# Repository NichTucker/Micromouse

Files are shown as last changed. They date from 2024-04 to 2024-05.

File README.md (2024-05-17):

# Micromouse
## Overview
Welcome to our Micromouse project repository. This repository contains all the necessary files and documentation related to our project, including PCB design files, reports, etc..

## Project Description
Our project involves designing the power subsystem and the sensing subsystem for the micromouse, which is essentially a maze-solving robot. We are focusing on designing the hardware components.

## Subsystems
### Power Subsystem
Responsible for powering and controlling the power supplied to the entire system, running the motors of the micromouse and charging the battery that powers the mouse.
### Sensing Subsystem
The sensor subsystem is responsible for detecting objects and ensuring that the micromouse maintains proper alignment within the maze pathways by sensing the walls around it.

The sensing subsystem folder contains all the necessary files and documentation for the design and implementation of the sensor subsystem. These being the datasheets of the non-passive components used, LaTeX and PDF design report, KiCad schematics and files, the gerber files and the code used to test if the micromouse can sense walls to the left, right and front of it.

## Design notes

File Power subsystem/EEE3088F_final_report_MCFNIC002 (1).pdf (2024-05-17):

# Interim Design Report

Micromouse Power Subsystem


Prepared by:
Nicholas McFarland
MCFNIC002

Prepared for:
EEE3088F
Department of Electrical Engineering University of Cape Town

May 17, 2024

# Declaration

1. I know that plagiarism is wrong. Plagiarism is to use another’s work and pretend that it is one’s own.
2. I have used the IEEE convention for citation and referencing. Each contribution to, and quotation in, this report from the work(s) of other people has been attributed, and has been cited and referenced.
3. This report is my own work.
4. I have not allowed, and will not allow, anyone to copy my work with the intention of passing it off as their own work or part thereof.

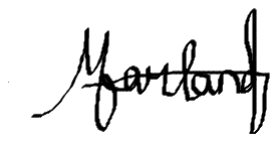
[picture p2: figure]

May 17, 2024

Nicholas McFarland | Date

ii

# Contents

1 Introduction | 1
2 Requirements Analysis | 2
3 Subsystem Design | 5
4 Acceptance Testing | 11
5 Conclusion | 18
Bibliography | 19

iii

# Chapter 1

# Introduction

### 1.1 Problem Description

This year’s design project aims to have a pair of students design and build a micromouse capable of solving a maze. The mouse begins at a starting position outside of the maze and is considered to have ‘solved’ the maze if it reaches the square opening in the middle of the maze.

Figure 1.1: Typical maze that a micromouse should be able to solve

The mouse’s final design consists of a motherboard, processor board, motors, wheels, power, and sensing subsystem. Both the motherboard and processor board will be responsible for most of the mouse’s information processing. The power and sensing subsystems are not provided, and so still need to be designed. The motherboard, processor board, wheels, and motors are provided by the course.

This report provides an in-depth analysis of the designed power subsystem, which is responsible for providing power to all the aforementioned systems and subsystems, as well as driving the motors of the mouse.

### 1.2 Scope and Limitations

The designed circuit board uses a single 1S1P battery to power all parts of the system of the micromouse. It must be able to operate 2 motors at rated current and voltage and provide an analog connection that provides information to the processor regarding the battery’s current voltage and charge state. It must be able to charge the battery from an external 5V input voltage and house an ON/OFF switch that can control the power supply to the system.

Besides the connections between the power subsystem’s pin headers and motherboard, this project provides no detail into the other subsystems of the overall micromouse. It does not provide any coding required to operate the other subsystem/s.

The shape of the PCB design must feature a tab with dimensions that prevent it from obstructing the motor connections or colliding with any of the motherboard connections. The design consists of a battery with a maximum voltage of 4.2V, so any selected component cannot have an operating voltage that exceeds this. The cost of producing 2 boards may not exceed $30 when ordered, so the cost per board may not exceed $15. All components selected for designing the system must be readily available on JLCPCB [1]. Finally, the design must be suitable for testing any potential problem points on the board and feature alternative options to prevent these problems.

### 1.3 GitHub Link

https://github.com/NichTucker/Micromouse

# Chapter 2

# Requirements Analysis

### 2.1 Requirements

The requirements for a micromouse power module are described in Table 2.1.

Table 2.1: User and functional requirements of the power subsystem.

Req. ID | Description
R01SWT | Design must be able to switch the micromouse ON and OFF
R02SWT | When the mouse is OFF, current drawn by battery < 500uA
R01PWR | Design powers the entire micromouse and drive the 2 motors used to drive the wheels
R01CHG | Charge the battery from an input pin
R02CHG | Recommended charge at 0.5C (Capacity) for battery
R01ADC | Provides information on the battery’s voltage and sense of state of charge (SoC)
R01PCB | Design must be able to fit on the motherboard without colliding with any of the other
| systems or the motors

### 2.2 Specifications

The specifications, refined from the requirements in Table 2.1, for the micromouse power module are described in Table 2.2.

Table 2.2: Specifications of the power subsystem derived from the requirements in Table 2.1.

Spec. ID | Description
S01SWT | Design utilizes a physical switch to provide the mouse with the ability to connect and
| disconnect the battery from the rest of the mouse
S02SWT | When the switch is in its OFF state and the battery is disconnected from the circuit, the
| current drawn by the battery must be < 500uA
S01PWR | Design uses the Battery LiPo 800mAh 3.7V (https://www.robotics.org.za/802540) to power all the systems of the micromouse and
| uses a dual bridge motor to operate the motors, each rated at 200mA and 3.7V
S01CHG | Circuit uses a Li-Po battery charger with a 5V operating input voltage
S02CHG | Drawn current < 400mA when charging
S01ADC | Voltage divider circuit to provide batter’s state of charge (SoC), as well as ensure the
| maximum input voltage < 3.3V
S01PCB | 2x8 pin header with 2.54mm pin pitch. The height of the tab > 18mm and the width of the
| tab < 35mm to prevent collision with the motors

2.3. Testing Procedures

### 2.3 Testing Procedures

A summary of the testing procedures [2] detailed in chapter 4 is given in Table 2.3.

Table 2.3: Testing Procedures

Testing ID | Description
AT01SWT | Switch provides discreet ON/OFF states
AT02SWT | Quiescent current less than maximum rated
AT01PWR | Each motor reaches its operating current of 200mA
AT02PWR | Each motor reaches its operating voltage of 3.7V
AT01CHG | Charging circuit charges battery
AT02CHG | Battery draws < 400mA when charging and the rest of the
| circuit is connected
AT01ADC | Pin M210 (BATT_ADC) provided with scaling analog volt-
| age
AT01PCB | Height and width of PCB tab smaller than area limited by
| motor.

### 2.4 Traceability Analysis

To show how the requirements, specifications and testing procedures all link, Table 2.4 is provided.

Table 2.4: Requirements Traceability Matrix

# | Requirements | Specifications | Acceptance Test

1 2 3 4 5 6 7 8 | R01SWT R02SWT R01PWR R01BAT R01CHG R02CHG R01ADC R01PCB | S01SWT S02SWT S01PWR S01BAT S01CHG S02CHG S01ADC S01PCB | AT01SWT AT02SWT AT01PWR, AT02PWR AT01BAT AT01CHG AT02CHG AT01ADC AT01PCB

### 2.4.1 Traceability Analysis 1

From R01SWT, the design must be able to switch the micromouse on and off. This is where S01SWT is derived, as it refines R01SWT to incorporate a physical switch to turn the micromouse on and off. This can be tested through AT01SWT, which tests that the design can disconnect the battery from the rest of the circuit, providing discreet ON/OFF states.

### 2.4.2 Traceability Analysis 2

R02SWT states that the current drawn by the battery when the mouse is off must be < 500uA. From this S02SWT specifies that this is the current in the case when the switch is off and the battery is

2.4. Traceability Analysis

disconnected from the circuit. This current is tested through AT02SWT, which is implemented to measure the quiescent current of the subsystem.

### 2.4.3 Traceability Analysis 3

From R01PWR the design must be able to power the entire micromouse and drive the motors. S01PWR builds on this, specifying that the design must use the Battery LiPo 800mAh 3.7V (https://www.robotics.org.za/802540) to provide power to the different systems and should use a dual H-bridge motor driver to operate the motors. These are tested through AT01PWR and AT02PWR, which test that the motors reach their correct operating currents and voltages.

### 2.4.4 Traceability Analysis 4

R01CHG states that the design must be able to charge the battery from an input pin. From this S01CHG can be derived as it provides more insight into the charging. It must use a Li-Po battery charger with a 5V operating input voltage, as this will be the provided charging voltage by the STM. This is tested by AT01CHG which tests that the circuit can charge the battery.

### 2.4.5 Traceability Analysis 5

From R02CHG, since the battery must charge at 0.5C, S02CHG is derived as it specifies that to meet this requirement the battery must draw < 400mA when charging and still be connected to the rest of the circuit. This is tested through AT02CHG, where the charging current is measured.

### 2.4.6 Traceability Analysis 6

R01ADC requires the design to provide information on the battery’s current voltage and state of charge. S01ADC provides more insight into this, describing the means to which this is met and that the maximum analog voltage < 3.3V. This is tested through AT01ADC, where this voltage is measured to ensure that it scales correctly.

### 2.4.7 Traceability Analysis 7

From R01PCB the design must be able to fit on the motherboard without any collisions. S01PCB is derived from this and provides more detail as to the specified dimensions that the PCB must be to prevent any collisions. This is tested through AT01PCB, which tests that the dimensions of the PCB are smaller than the area limited by the motors.

# Chapter 3

# Subsystem Design

### 3.1 Design Decisions

### 3.1.1 Final Design

*From component browsing on JLCPCB it was found that the 0603 package resistors and capacitors were abundantly stocked, so

unless explicitly stated otherwise all resistors and capacitors were selected from these packages.*

Motor Driver

To turn the wheels the power subsystem requires a circuit design to drive the motors. Normally it would be easiest to drive the motor with a solo H-bridge, but with 2 motors needing to be driven simultaneously, this would not suffice. If the motors are to be driven at the same speed, each H-bridge would need identical voltages. This is practically impossible to achieve with 2 H-bridges, but this problem is solved if a dual H-bridge is used instead.

When checking JLCPCB, the options for dual H-bridge motor drivers were extremely limited, as most of the components

had low stock. The only ones that had enough stock to even consider using were the DRV8833 drivers. This, in conjunction

with their datasheets made the DRV8833s the best option for driving the micromouse. The selection process below

consists of tabulated potential choices from JLCPCB and selecting the most viable option:

Table 3.1: Dual bridge motor driver ICs

Possible solu-tion | Rated Supply Voltage (V) | Rated Supply Current (A) | Price per IC($) | Availability | Dimensions (mm x mm)
DRV8833PWP (https://wmsc.lcsc.com/wmsc/upload/file/pdf/v2/lcsc/2303020200_Texas-Instruments-DRV8833PWP_C1556089.pdf) | 2.7 - 10.8 | 1.5 | 1.1790 | 27 | 5 x 6
DRV8833PWPR (https://wmsc.lcsc.com/wmsc/upload/file/pdf/v2/lcsc/1810151712_Texas-Instruments-DRV8833PWPR_C50506.pdf) | 2.7 - 10.8 | 1.5 | 0.6660 | 9631 | 5 x 6
DRV8833RTYR (https://wmsc.lcsc.com/wmsc/upload/file/pdf/v2/lcsc/1810010132_Texas-Instruments-DRV8833RTYR_C154936.pdf) | 2.7 - 10.8 | 1.5 | 1.185 | 1315 | 4 x 4

from Table 3.1, the DRV8833PWPR (https://wmsc.lcsc.com/wmsc/upload/file/pdf/v2/lcsc/1810151712_Texas-Instruments-DRV8833PWPR_C50506.pdf) was chosen, because of the following:

- Meets the required rated voltage and current
- Much cheaper option than option 1 and option 3
- Readily available (higher stock than 1 and 3)
- The datasheet provides a typical circuit diagram of how to implement the device

*Note that the DRV8833PWPR (https://wmsc.lcsc.com/wmsc/upload/file/pdf/v2/lcsc/1810151712_Texas-Instruments-DRV8833PWPR_C50506.pdf) IC’s datasheet provides a suitable circuit schematic for setting up the driver’s connections.*

All capacitors were chosen at E24 values and added to prevent any AC noise from interfering with the motor driver circuit.

3.1. Design Decisions

Battery Management

The power subsystem requires battery-charging capabilities to charge the battery powering the rest of the mouse. Due to the requirements of the design the charger can only be powered by a 5V supply. This was taken into account when selecting potential solutions.

The easiest way to implement this charging is with a battery-charger IC. Using one of these, instead of designing one from scratch provides a much more reliable, stable and safe charge to the battery.

Once again, when looking at the options on JLCPCB, most of the charger ICs were too low stocked to even be considered,

but the TP4056 family provided ICs that operated at the required voltages (4.2V maximum battery charge voltage

charged with a 5V input) and were readily stocked at the time of ordering. The following ICs were considered for the

design:

Table 3.2: battery management ICs

Possible solution | JLCPCB part # | Rated Input Voltage (V) | Quietient current/Iq (uA) | Price per IC($) | Availability | Dimensions (mm x mm)
TP4056 | C725790 (https://wmsc.lcsc.com/wmsc/upload/file/pdf/v2/lcsc/2311091738_UMW-Youtai-Semiconductor-Co---Ltd--TP4056_C725790.pdf) | 4.0 - 6.5 | 35 | 0.0620 | 29409 | 4 x 5
TP4056 | C17702041 (https://wmsc.lcsc.com/wmsc/upload/file/pdf/v2/lcsc/2309121405_HXY-MOSFET-TP4056_C17702041.pdf) | 4.5 - 8.0 | 55 | 0.0587 | 10658 | 5 x 5
TP5000X-4.2-ESOP8 | C5447152 (https://wmsc.lcsc.com/wmsc/upload/file/pdf/v2/lcsc/2304251410_TOPPOWER-Nanjing-Extension-Microelectronics-TP5000X-4-2-ESOP8_C5447152.pdf) | 4.0 - 9.0 | 180 | 0.2465 | 5022 | 5 x 6

From Table 3.2, the first solution (C725790) was chosen. The reasons are as follows:

- Cheaper than option 2.
- Largest available supply.
- Smallest component (reduces PCB size).
- Lowest Iq ensures lowest possible current when mouse is active.

The charging current is controlled by the Rprog resistor. From the given equation in the datasheet:

Ibat =

Vprog

Rprog

1200

Setting Rprog at 1600 Ω ensures Ibat is (750mA) which is less than the maximum rated current (1A) and that the resistor is of E24 value. The rest of the circuit was designed with the aid of a typical charging circuit on the datasheet of a similar IC [TP4056]. (https://dlnmh9ip6v2uc.cloudfront.net/datasheets/Prototyping/TP4056.pdf)

*The selected IC has built-in voltage regulation and protection, so this was not needed in the design

Analog Sensing

This consists of a voltage divider circuit that reduces the battery’s read voltage to a maximum of 3V3 (ADC pin’s required voltage).
Since the battery has a maximum of 4.2V, simply feeding this into the ADC pin could break it, so the divider circuit must ensure Vout ≤ 3.3V. from the equation of a voltage divider:

Vout = Vin

R7
R5 + R7

Setting R5 = 10KΩ and R7 = 33KΩ, Vout is set at 3.22V which is safely below its rated voltage. By setting these resistors

to a magnitude of more than 10³
, it ensures that the current in this circuit is minuscule.

3.1. Design Decisions

Circuit Switching

To ensure that the battery is fully disconnected from the circuit, the switch is connected directly after the battery (Battery -> switch -> circuit). Some of the viable JLCPCB switches that match these requirements are tabulated below:

Table 3.3: Possible switches available on JLCPCB

Possible solu-tion | Type | Rated Volt-age (V) | Rated Cur-rent (mA) | Price per Switch($) | Availability | Dimensions (mm x mm)
EG1224 (https://wmsc.lcsc.com/wmsc/upload/file/pdf/v2/lcsc/1912111437_E-Switch-EG1224_C273395.pdf) | Slide | 15 | 500 | 0.7695 | 70 | 7 x 12
PS-5850A-6PL (https://wmsc.lcsc.com/wmsc/upload/file/pdf/v2/lcsc/2012062037_G-Switch-PS-5850A-6PL_C963201.pdf) | Push (Latching) | 30 | 500 | 0.1185 | 1514 | 5 x 5
SS12D07VG4 087 (https://wmsc.lcsc.com/wmsc/upload/file/pdf/v2/lcsc/2201121830_SHOU-HAN-SS12D07VG4-087_C2939726.pdf) | Slide | 50 | 500 | 0.0278 | 28097 | 8 x 9
YTSPS-22E58LM (https://wmsc.lcsc.com/wmsc/upload/file/pdf/v2/lcsc/2201121900_YIYUAN-YTSPS-22E58LM_C2941005.pdf) | Push (Latching) | 50 | 500 | 0.1588 | 1705 | 5 x 8

From Table 3.3 the PS-5850A-6PL was chosen. The reasons are as follows:

- Meets regulated voltage ( > 4.2V) and regulated current ( > 400mA).
- Push switches take up less horizontal space (reduce PCB space).
- Cheapest push switch.

Final design

The final design incorporates all the different design decisions to meet the requirements. It houses the battery that powers the micromouse, provides a physical latching switch to control the battery supply, a motor driver to drive the motors, a battery charger to charge the battery supply, and an ADC circuit to provide analog sensing.

The design choices were made to increase the efficiency of the power subsystem [3]. This includes selecting parts that; are

relatively cheaper when compared to similar components, consume less current than other components/consume as close

to the required current as possible, and have smaller dimensions which helps to reduce the size of the final PCB (and in

doing so helps keep the micromouse’s center of rotation as close to the front as possible).

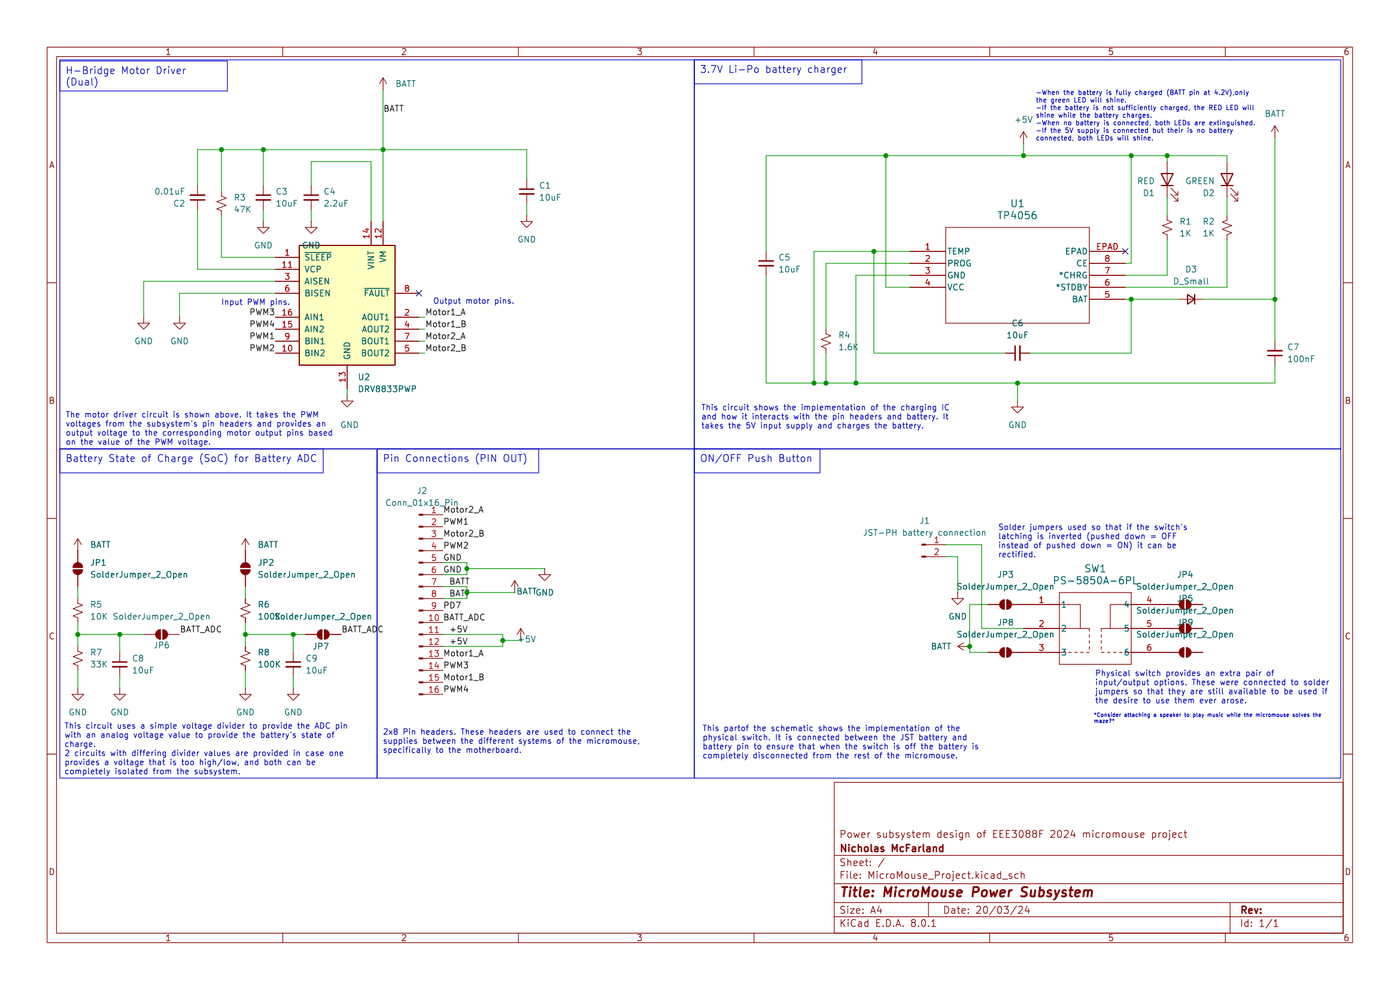
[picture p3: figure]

Figure 3.1: Schematic

3.2. Failure Management

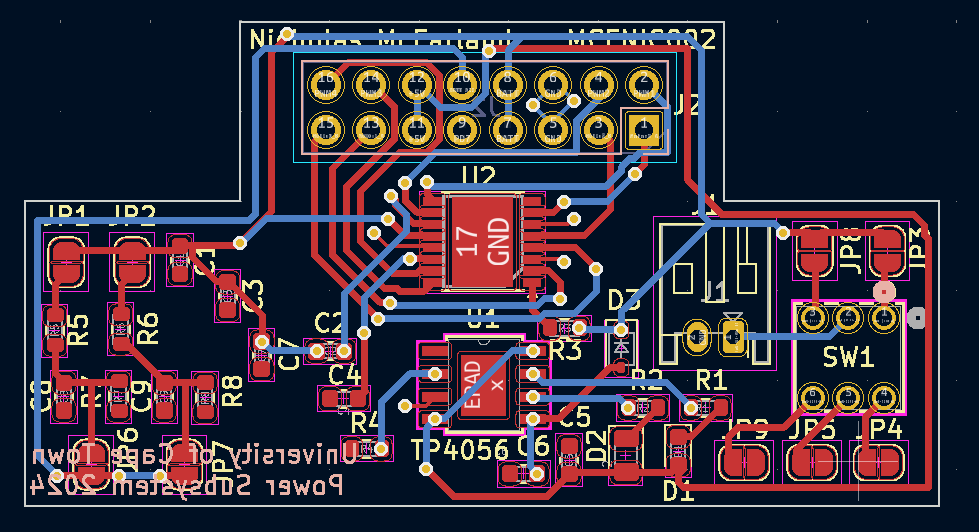
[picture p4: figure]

(a) Front PCB (with ground pours omitted for clearer view of tracks)

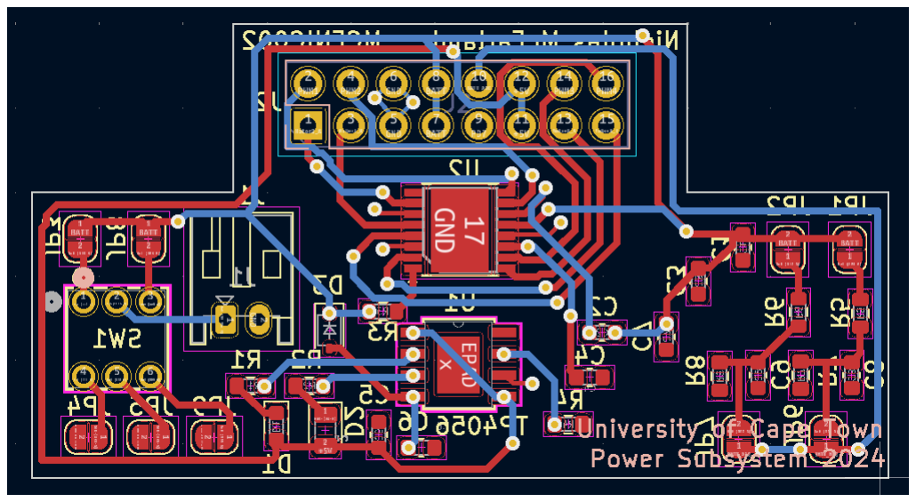
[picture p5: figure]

(b) Back PCB (with ground pours omitted for clearer view of tracks)

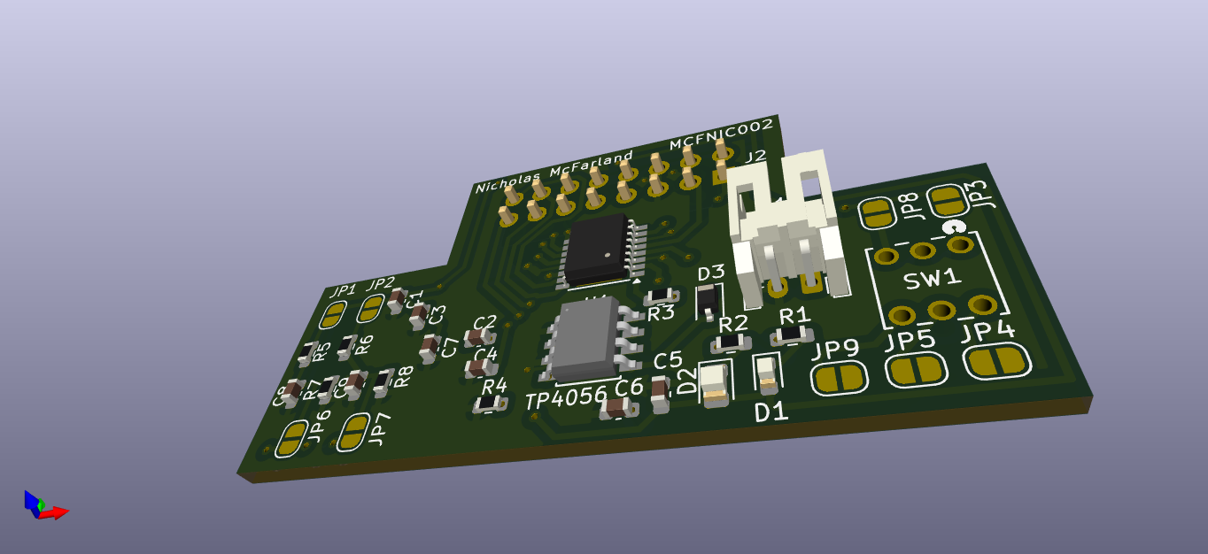
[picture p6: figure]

(c) 3D PCB (with all components populated to depict the final PCB layout)

Figure 3.2: Final PCB design layouts

### 3.2 Failure Management

Tthe following measures were taken to reduce the possible failures that the PCB could face after production or to bypass

any design decisions that were made with some uncertainty:

Table 3.4: Failure Management Table

Name | Description
Track current han-dling [4] | Since the motors carry currents too large for standard track width, track width was increased. All tracks’ widths were increased, due to uncertainty as to which tracks would carry the highest currents.
Battery/5V Tracks | Tracks leading directly from the switch and 5V charging input were put as close to the edge of the PCB as possible to minimize any interference with other tracks. This is because they are likely to draw high currents.
Switch placement | Switch placed directly after the battery to ensure the entire circuit is cut off from power when the switch is on.
Switch solder bridges | Due to the vague diagram on the datasheet, uncertainty arose concerning pin connections. Each connection is joined with a solder bridge to ensure the right connections are made in the future.
Additional analog voltage-divider | In case the voltage-divider output voltage is too close to the rated ADC pin, a second one was designed with a much lower output voltage (half of the maximum battery voltage)
Analog solder bridges | Both circuits are separated from battery input and pin output by solder bridges. This ensures that the correct one can be connected, whilst the unused one does not draw any current from the battery (remains completely idle).
E24 component calculation round-ing | All calculated E24 component values rounded to ensure the relative currents/voltages are well below rated maximums and well above rated minimums.

3.3. System Integration and Interfacing

### 3.3 System Integration and Interfacing

To aid in describing the integration of the subsystem with the rest of the system, the following system integration table is provided:

Table 3.5: Interfacing specifications

Interface | Description | Pins / Output

BAT_IN

Battery supply input to
power subsystem
- Li-Po battery terminals to JSTPOS, JSTNEG

BAT_OUT

Battery supply output to micromouse system

- M207, M208 to the processor through F207, F208

BAT_ADC

Battery analog state of
charge output to micromouse system
- M210 to STM Pin 48 through F210

5V

External 5V supply input for charger

- M211, M212 to processor through F211, F212

GND

ground connection between
subsystem and processor
- M205, M206 to ground through F205, F206

MTR01

DRV8833PWPR interfacing
with motor1 output and
PWM input
- Motor1_A (M213) to the physical side A of motor 1 through

F213
- Motor1_B (M215) to the physical side B of motor 1 through F215
- PWM3 (M214) to STM PC6-9 (unknown at this point) through F214
- PWM4 (M216) to STMPC-9 (unknown at this point) through F216

MTR02

DRV8833PWPR interfacing
with motor2 output and
STM logic input
- Motor2_A (M201) to the physical side A of motor 2 through

F201
- Motor2_B (M203) to the physical side B of motor 2 through F203
- PWM1 (M202) to STM PC6-9 (unknown at this point) through F202
- PWM2 (M204) to STMPC-9 (unknown at this point) through F204

3.3. System Integration and Interfacing

System Block Diagram

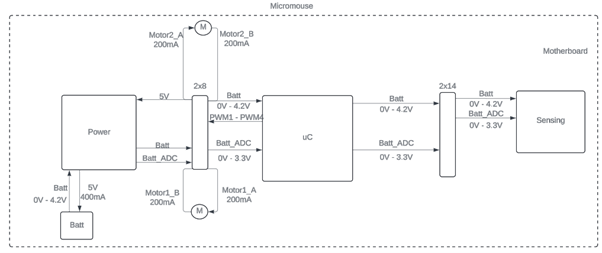
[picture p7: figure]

Figure 3.3: High-level block diagram showing subsystem’s link into the larger system. (Information on sensing inputs/outputs limited)

# Chapter 4

# Acceptance Testing

### 4.1 Tests

Table 4.1: Subsystem acceptance tests

Test ID | Description | Testing Procedure | Pass/Fail Criteria

AT01SWT

Test that the switch connects the battery to the system when LATCHED and
disconnects it when RE-LEASED
- Solder JP3 and connect 4.2V DC voltage supply at 4.2V to JSTPOS
- use a multimeter to measure the voltage at M207 / M208
- If inverted switching, desolder JP3 and solder JP8. Provide the same voltage to JSTPOS and measure the voltage at M207 M208

Pass if the voltage at pin M207/M208 = 4.2V when
LATCHED and 0V when
RELEASED

AT02SWT

The current drawn by the
battery when the switch is RELEASED is less than its
maximum rated to ensure
minimal leakage
- Disconnect the motors
- Connect ammeter between LiPo positive terminal and JST-POS
- LATCH switch.

Pass if current measured is < 500uA

AT01PWR

Test that the motors reach their operating current to ensure they have enough potential torque.

- Connect Motor1 side B to M215 and side A to the positive terminal of the ammeter Connect the negative terminal to M213.
- Connect 4.2V DC power supply to M207 / M208
- Set switch to LATCH
- Repeat for Motor2, but changing connections to motor2 equivalents (M203, M201)

Pass if currents measured
for BOTH motors is at least 200mA - 5%

AT02PWR

Test that the motors reach their operating current to ensure they have enough potential speed.

- Connect Motor1 side B to M215 and side A to M213. Connect multimeter across M215 and M213
- Connect 4.2V DC power supply to M207 / M208
- Set switch to LATCH
- Repeat for Motor2, but changing connections to motor2 equivalents (M203, M201)

Pass if voltage measured for BOTH motors > 95% of input voltage (V > 4V)

AT01CHG

The battery’s voltage increases to its maximum capacity when the 5V pin is
powered and the battery is connected
- Connect battery to JSTPOS / JSNEG and press switch down to ON state.
- Use DC power supply to provide 5V to M211 / M212. Check that the green LED is ON.
- Use a multimeter to measure the voltage at M207/ M208.

Pass if voltage = 4.2V +-
5%

AT02CHG

Battery draws < 400mA
when charging and the rest of the circuit is connected, to charge the battery at the design’s rate of charge
- Connect the positive battery terminal to the positive ammeter lead and the negative lead to JSTPOS. Connect the negative terminal to JSTNEG
- Connect 5V DC supply to M211 / M212 and LATCH switch.

Pass if the current measured < 400mA

AT01ADC

Analog | sub-circuit | pro-
duces a scaling analog
voltage at a maximum of
3.3V when 4.2V is provided to the BATT pin
- Solder JP1 and JP6
- Connect multimeter to M210 and DC supply voltage to M207 / M208
- Starting at 0V, increase voltage to 4.2V
- If multimeter reading > 3.3V, desolder JP1, JP6 and solder JP2, JP7 and repeat steps

Pass if measured voltage
scales with DC supply voltage AND measured voltage
< 3.3V when DC supply
voltage = 4.2V

AT01PCB

Testing the height and
width of the PCB tab to
ensure that it does not collide with the motors
- Use a ruler to measure the height and width of the tab
- Place over demo mouse’s power subsystem outline

Pass if height > 18mm and
width < 35mm OR PCB
fits into demo outline

4.2. Critical Analysis of Testing

### 4.2 Critical Analysis of Testing

The following tests were selected due to; their importance in the overall project, and the roles that they played in the demonstration of the PCB:

Table 4.2: Subsystem acceptance test results

Test ID | Description | Result
AT01PWR | Motors reach operating currents | Pass
AT02PWR | Motors reach operating voltage | Pass
AT01CHG | Battery charges fully from charger | Fail
AT02CHG | Battery draws < 400mA when charg-
| ing | Pass
AT01ADC | Circuit produces scaling ADC with
| a maximum < 3.3V | Pass

### 4.2.1 AT01PWR

Aim

The AT01PWR test is carried out to measure the current that the motors draw when the circuit is in full operation. The currents that the motors draw determines the torque that they experience, so they require their rated current to produce a torque sufficient to run the motors. This rated current is the current that AT01PWR tests for.

Testing

The testing procedures for AT01PWR are as follows:

1. Connect side B of Motor1 to pin M215 and side A of Motor1 to the positive terminal of the ammeter. Connect the negative terminal to pin M213. This connects the ammeter in series to the motor to measure the current.
2. Set the DC voltage supply to 4.2V (representing the battery’s maximum voltage) and provide this voltage to pins M207/M208. This represents the battery at its maximum voltage.
3. Push the switch down (set to LATCH).
4. Record the measurement displayed on the ammeter.
5. repeat steps 1-4 for Motor2 to record its current.

*Note that for Motor2: M215 (Mot1) = M203 (Mot2), M213 (Mot1) = M201 (Mot2)*

Results

During testing, the following results were recorded:

- Motor1 current - 199mA
- Motor2 current - 198mA

4.2. Critical Analysis of Testing

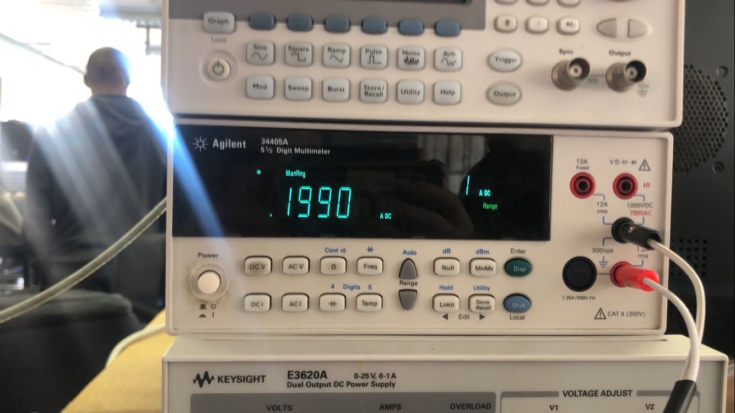
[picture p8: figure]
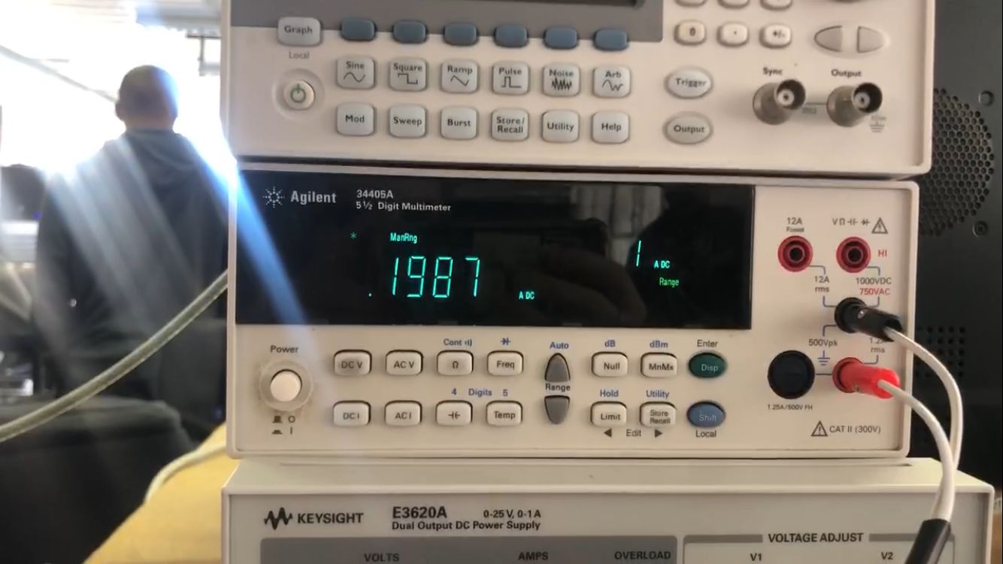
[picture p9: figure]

(a) Measured current of Motor1 | (b) Measured current of Motor2

From these results, it can be concluded that AT01PWR was passed, as the PCB produces the rated motor current of 200mA per motor.

### 4.2.2 AT02PWR

Aim

The AT02PWR test is carried out to measure the voltage across the motors when the circuit is in full operation. The voltages that the motors operate at determine the speed at which they rotate, so they require their rated voltage to produce a speed fast enough to run the motors. This rated voltage is the voltage that AT02PWR tests for.

Testing

The testing procedures for AT02PWR are as follows:

1. Connect side B of Motor1 to pin M215 and side A of Motor1 to pin M213. Connect the positive terminal of the multimeter to pin M215 and the negative terminal to ground. This connects the multimeter in parallel to the motor to measure the voltage across the motor.
2. Connect the DV voltage supply to M207/M208 and set its voltage to 4.2V. Once again, this represents the battery connection at its maximum voltage.
3. Push the switch down (set to LATCH).
4. Record the measurement displayed on the multimeter.
5. repeat steps 1-4 for Motor2 to record its voltage.

*Note that for Motor2: M215 (Mot1) = M203 (Mot2), M213 (Mot1) = M201 (Mot2)*

Results

During testing, the following results were recorded:

- Motor1 voltage - 4.2V
- Motor2 current - 4.2V

4.2. Critical Analysis of Testing

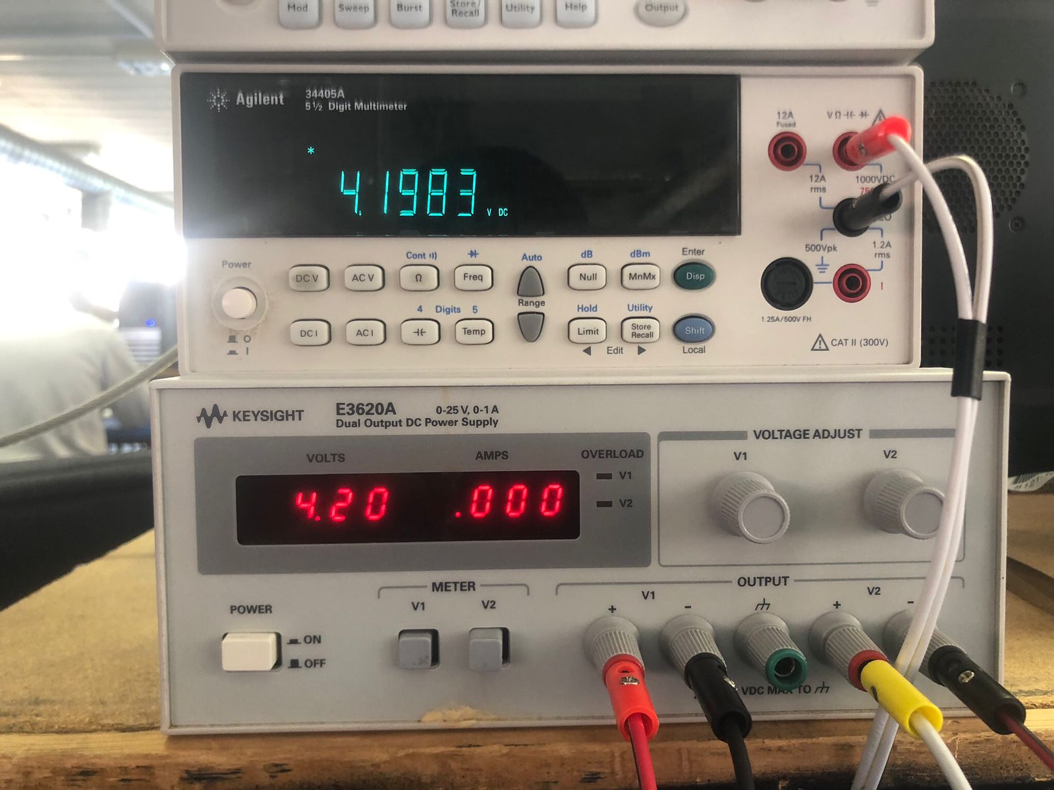
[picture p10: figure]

(a) Measured voltage of Motor1 | (b) Measured voltage of Motor2

From these results, it can be concluded that AT01PWR was passed, as the PCB produces the required rated voltage of at least 95% of the input voltage (V > 4V) to each motor.

### 4.2.3 AT01CHG

Aim

The AT01CHG test is carried out to determine that the battery charging section of the PCB, when powered by a 5V input voltage supply, can charge the battery to its maximum storage voltage of 4.2V.

Testing

The testing procedures for AT01CHG are as follows:

1. Connect the battery’s positive terminal to JSTPOS and the negative terminal to JSTNEG. Push the switch down to LATCH.

*Note that no battery was provided for testing, so a resistor-capacitor circuit was used instead to produce the same charging effect as the battery.*

2. Connect the DC voltage supply to pin M211/M212 and set the voltage to 5V.
3. Connect the positive terminal of the multimeter to pin M207/M208.
4. Ensure that the green LED is ON. This means that the circuit is charging correctly.
5. Record the value displayed on the multimeter.

Results

During testing, the following results were recorded:

- maximum battery voltage (Lab testing) - 3.866V
- maximum battery voltage (Demo) - 4.18V

4.2. Critical Analysis of Testing

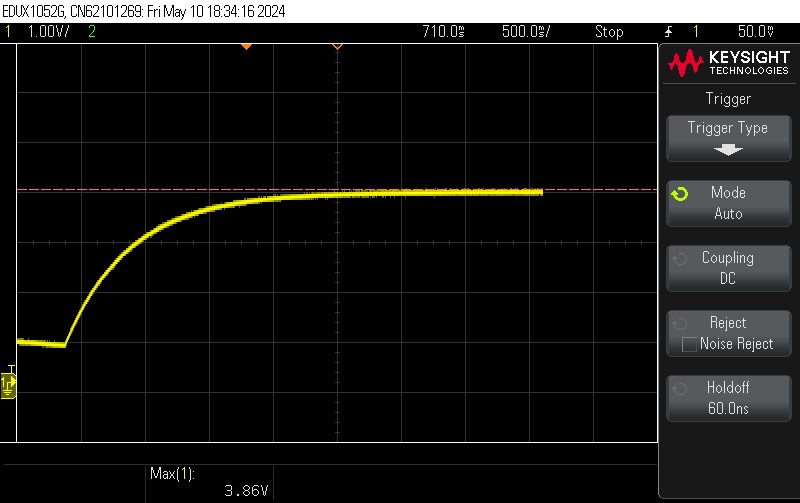
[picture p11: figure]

Figure 4.3: Voltage across RC circuit as a function of time.

Although this result means that the test failed in the lab, it should be noted that the circuit used to mimic a charging battery would not produce the same voltage as an actual battery. The test carried out during the demonstration, with the proper battery, produced the correct voltage and so this test case failed in the lab but passed in the demo, as the battery was able to reach its maximum voltage of 4.2V when charged.
The voltage drop recorded is due to the Schottky diode connected between the pin M207/M208 and the output of the charging IC.

### 4.2.4 AT02CHG

Aim

The AT02CHG test is carried out to determine the current drawn by the battery when it is charging, specifically if it is less than its rated current draw. This rated current draw ensures that the battery charger meets the IC’s rate of charge.

Testing

The testing procedures for AT02CHG are as follows:

1. Connect the positive terminal of the battery to the positive terminal of the ammeter and the negative lead of the ammeter to the JSTPOS pin.
2. Connect the DC voltage supply to pin M211/M212 and set the voltage to 5V.
3. Push the switch down to LATCH.
4. Record the ammeter display.

Results

During testing, the following results were recorded:

- Drawn battery current - 383mA

4.2. Critical Analysis of Testing

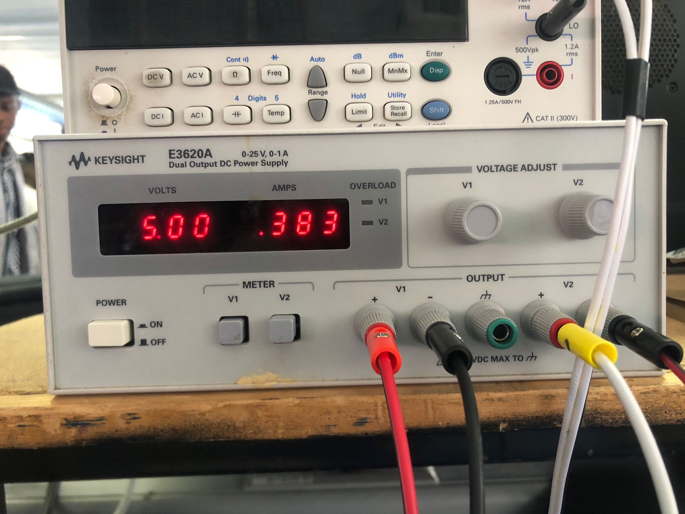
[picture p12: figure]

Figure 4.4: Drawn battery current.

From this result, it can be concluded that AT02CHG was passed, as the battery draws a current that is less than the rated current of 400mA, which ensures that the battery will charge at the correct rate.

### 4.2.5 AT01ADC

Aim

The AT01ADC test is carried out to determine if the voltage produced by the ADC circuit meets the required scaling, and that its maximum output is less than the maximum voltage that the ADC pin (M210) should hold.

Testing

The testing procedures for AT01ADC are as follows:

1. Solder JP1, JP6 to connect divider 1 or JP2, JP7 to connect divider 2.
2. Connect the positive terminal of the multimeter to pin M210.
3. Connect the DC supply voltage to pin M207/M208. This voltage represents the battery’s changing voltage.
4. Starting at 0V, slowly increase the input DC voltage and watch the multimeter display. Once the input voltage reaches 4.2V, leave the voltage and record the multimeter display.

Results

During testing, the following results were recorded:

- pin M210 voltage when 3.7V is at pin M207/M208 - 2.83V.
- pin M210 voltage when 4.2V is at pin M207/M208 - 3.22V

4.2. Critical Analysis of Testing

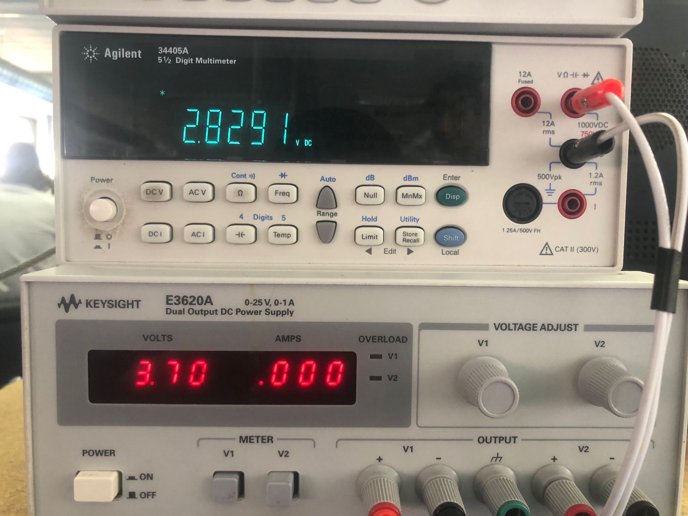
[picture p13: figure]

(a) Voltage at pin M210 at 3.7V battery voltage.

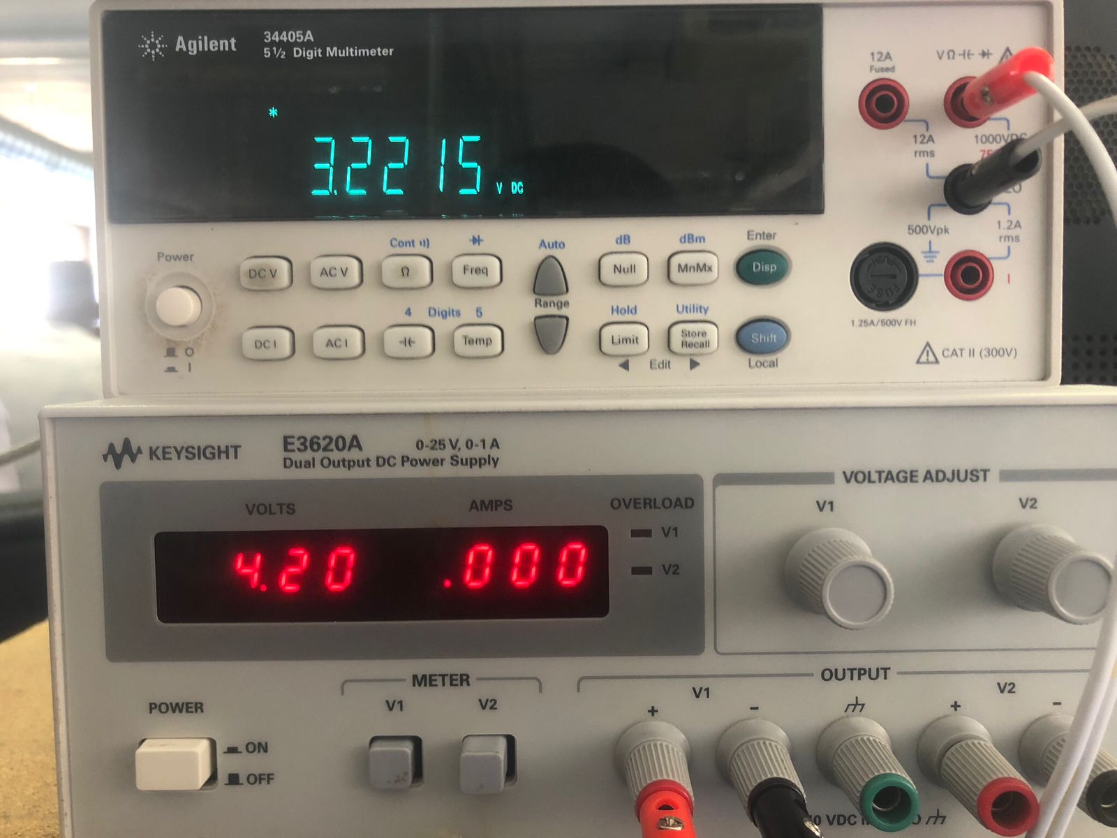
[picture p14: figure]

(b) Voltage at pin M210 at maximum 4.2V battery voltage.

From these results, it can be concluded that AT01ADC was passed, as the design provides a scaling analog voltage to pin M210 as the battery voltage increases, with a maximum ADC pin voltage < 3.3V at the battery’s maximum voltage.

# Chapter 5

# Conclusion

This report provides an in-depth analysis of the power subsystem designed to power a maze-solving micromouse and operate its motors through use of a single 1S1P battery. The system provides switchable power to all parts of the mouse’s system, charges the battery through an external 5V input supply voltage, provides motor control from logic input pins, and provides the motherboard with the ADC equivalent voltage of the battery.

The power distribution is handled through a latching switch connected to a battery pin. this pin is connected to the motherboard, where its voltage is accessible by the other systems. The design incorporates a charging IC to charge the battery with an external 5V input voltage and LEDs to indicate the state of charge when charging. It handles the operation of the motor through a dual H-bridge motor driver, which is capable of providing the motors with controllable logic voltage signals. Finally, it utilizes a simple voltage divider circuit to provide the ADC pin with a 3.3V logic equivalent voltage of the battery’s current state of charge.

The switch provides complete connection and disconnection between the battery and micromouse, which allows for minimal quiescent current. The dual H-bridge motor provides both motors with identical voltages and currents when powered with equivalent logic inputs, which allows the motors to operate synchronously. The ADC circuit provides a consistent scaling analog voltage to the ADC pin, with a maximum value less than the pin’s maximum allowable voltage.

### 5.1 Recommendations

Switching

The switch used in this design has a maximum current rating of 500mA and so cannot handle large currents (< 1A). This is important when powering the micromouse, as additional torque on the motors can draw significantly more current than it was originally designed for. This can be solved by using a MOSFET in conjunction with the switch, where the MOSFET can limit the current through the switch.

Component bypassing

From the battery charging section of the design choice, it was noticed that the Schottky diode provided an unwanted voltage drop. In the future, it would be better to have the option to short any components whose function is uncertain. This can be done with solder jumpers in parallel to the component, which can then be shorted to bypass the component.

# Bibliography

[1] [Online]. Available: https://jlcpcb.com/parts/all-electronic-components
[2] “Preventing pcb failure: Causes, symptoms, and maintenance tips.” [Online]. Available: https://www.pcbaservices.com/preventing-pcb-failure/
[3] “Kicad design pcb: Tips and tricks for successful printed circuit.” [Online]. Available: https://hillmancurtis.com/kicad-design-pcb/
[4] “Trace width calculator.” [Online]. Available: https://forum.kicad.info/t/trace-width-calculation/16091 (https://forum.kicad.info/t/trace-width-calculation/16091)

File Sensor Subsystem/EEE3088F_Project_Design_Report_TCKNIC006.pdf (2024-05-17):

# Project Design Report

Micromouse Sensor Subsystem

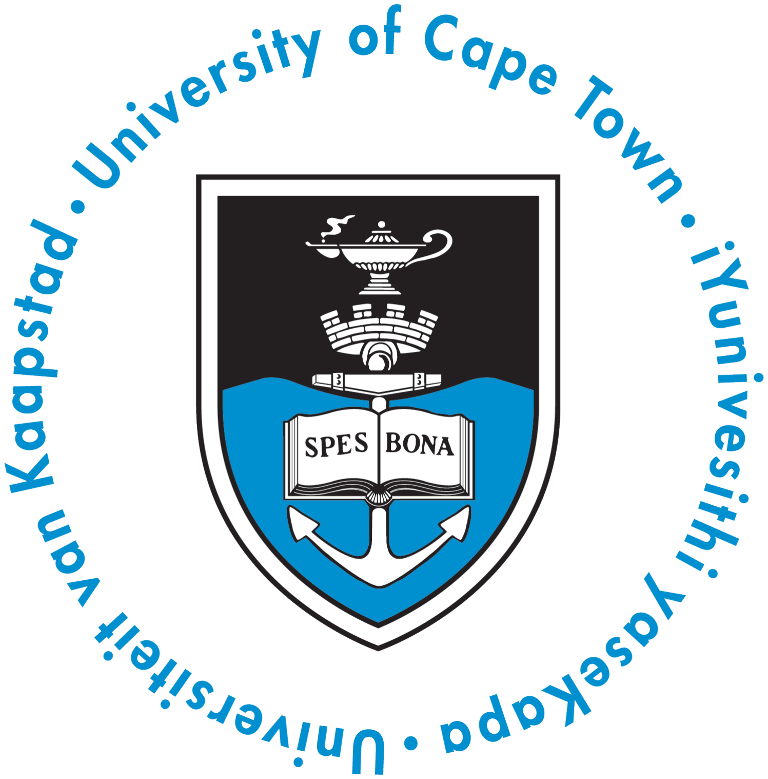
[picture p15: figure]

Prepared by:
Nicholas Tucker (TCKNIC006)

Prepared for:
EEE3088F
Department of Electrical Engineering University of Cape Town

May 17, 2024

# Declaration

1. I know that plagiarism is wrong. Plagiarism is to use another’s work and pretend that it is one’s own.
2. I have used the IEEE convention for citation and referencing. Each contribution to, and quotation in, this report from the work(s) of other people has been attributed, and has been cited and referenced.
3. This report is my own work.
4. I have not allowed, and will not allow, anyone to copy my work with the intention of passing it off as their own work or part thereof.

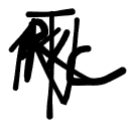
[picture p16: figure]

May 17, 2024

Nicholas Tucker

ii

# Contents

1 Introduction | 1
2 Requirements Analysis | 2
3 Subsystem Design | 5
4 Acceptance Testing | 11
5 Conclusion | 19
6 Bibliography | 20

iii

# Chapter 1

# Introduction

## 1.1 Problem Description

The project is focused on the development of the hardware for a micromouse, which is a small robotic vehicle designed to navigate and solve a maze autonomously. In order for the mouse to be successful, it needs to reach the finishing area within the maze. The project has been compartmentalised into four modules: the processor (which has a STM32L476 microcontroller), motherboard, sensing subsystem and power subsystem. The processor and motherboard modules have been designed prior. The third year engineering students have been tasked with designing the sensing subsystem and power subsystem in pairs. This design report will focus on the sensing subsystem, which is responsible for detecting objects and allowing the micromouse to traverse through the maze with proper alignment in the centre of a pathway. This project will not deal with the software of the sensor subsystem.

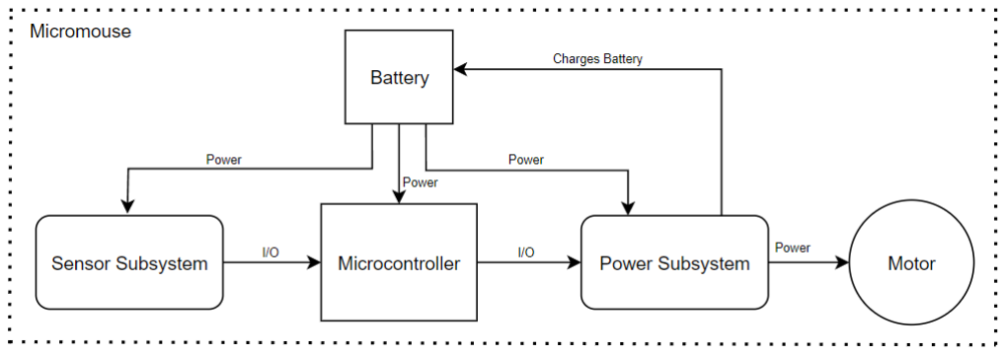
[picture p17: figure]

Figure 1.1: Simplified Context Diagram

## 1.2 Scope and Limitations

Scope of the report:

- Describe the specific objectives and goals of the sensing subsystem within the context of the overall project.
- Identify the requirements and specifications of the sensing subsystem.
- Explain how these requirements and specifications will be tested for.
- Discuss the decisions involving component selection, evaluating possible solutions and providing calculations used to design the sensing subsystem.
- Discuss how the PCB is designed to mitigate failure in the sensing-subsystem circuit design.
- Show how the sensing subsystem fits into the larger system.

Limitations of the report:

- A budget may have restricted the selection of components, potentially affecting the overall quality or performance of the system.
- The short timeframe (less than a semester) may have limited the depth of research, design iterations, and testing procedures, thereby impacting the comprehensiveness and robustness of the design.
- Although access to a lab with oscilloscopes and multimeters was available, other specialized equipment or facilities may have been lacking, limiting the range and quality of tests that could be implemented.

## 1.3 GitHub Link

Link to the shared repository on GitHub: https://github.com/NichTucker/Micromouse

# Chapter 2

# Requirements Analysis

## 2.1 Requirements

The requirements for the micromouse sensor module are described in Table 2.1.

Table 2.1: Requirements of the sensing subsystem.

Requirement ID | Description
R01 | System shall sense when an object is in front and by the sides of the
| micromouse.
R02 | Output of the system shall be consistent at different distances from an object.
R03 | Outputs of system shall be suitable for microcontroller.
R04 | Subsystem shall be power efficient when in operation and have mitigation
| means on the effects of ambient light on the system.
R05 | Components on PCB shall be accessible to be tested.
R06 | Total cost of PCB shall be within the budget.
R07 | Power shall be supplied by a battery.
R08 | PCB shall be small enough and be shaped such that the
| micromouse can fit in the pathway and turn through corners of the maze.
R09 | PCB shall not be too heavy.

## 2.2 Specifications

The specifications, refined from the requirements in Table 2.1, for the micromouse sensor module are described in Table 2.2.

Table 2.2: Specifications of the sensing subsystem derived from the requirements in Table 2.1.

Specification ID | Description
SP01 | Peak voltage at output increases when sensor is brought closer to an object.
SP02 | Peak voltage when sensor is 8 cms away from an object shall be greater than 2.5V
| with a range/consistency less than ±0.2V at the output.
SP03 | Peak voltage when sensor is 16 cms away from an object shall be within 0.9V and 1.7V
| with a range/consistency less than ±0.2V at the output.
SP04 | When no object is sensed, the voltage at the output shall be less than 0.5V with a range/
| consistency less than ±0.2V and output waveform shall have an amplitude of less than 0.1V.
SP05 | Output of sensor shall never be more than 3.3V.
SP06 | Emitter/sender of sensor shall be pulsed at a particular pulse width and duty cycle.
SP07 | Test points shall be placed across key components in order to measure their
| voltage w.r.t. ground.
SP08 | Total cost of two PCB boards shall be no more than 30 USD. This includes the PCB
| manufacture, the PCB assembly and the remaining budget for components.
SP09 | A Polymer Lithium Ion battery rated at 3.7V and 800mAh
| from Micro Robotics shall supply power to the system.
SP010 | The pathways in the maze are 200mm wide. Maximum length and width of PCB shall
| be smaller than 60mm, thereby leaving leeway for microcontroller to turn through corners.
SP11 | Mass of PCB shall not be more than 300g.

2.3. Testing Procedures

## 2.3 Testing Procedures

A summary of the testing procedures detailed in Chapter 4 is given below:

Acceptance Test ID | Description
AT01 | Voltage at output will be tested when sensor is moved closer to an object.
AT02 | Output voltage when sensor is 8 cms away from an object shall be measured.
AT03 | Output voltage when sensor is 16cm away from an object shall be measured.
AT04 | Output Voltage when no object is sensed shall be measured.
AT05 | Voltage regulator’s output voltages shall be measured w.r.t. ground.
AT06 | Pulse length and duty cycle of emitter and receiver shall be measured.
AT07 | Each test point on PCB shall be tested to ensure they are working correctly.
AT08 | Total cost of two PCB boards shall be calculated.
AT09 | Voltage across battery shall be measured.
AT10 | The dimensions of the PCB shall be measured.
AT11 | Mass of PCB shall be measured.

## 2.4 Traceability Analysis

Table 2.3 shows how the requirements, specifications and testing procedures all link:

Table 2.3: Requirements Traceability Matrix

# | Requirements | Specifications | Acceptance Test

1 2 3 4 5 6 7 8 9 | R01 R02 R03 R04 R05 R06 R07 R08 R09 | SP01 SP02, SP03, SP04 SP05 SP06 SP07 SP08 SP09 SP10 SP11 | AT01 AT02, AT03, AT04 AT05 AT06 AT07 AT08 AT09 AT10 AT11

### 2.4.1 Traceability Analysis 1

R01 states that the system shall sense when an object is in front and by the sides of the micromouse. From this SP01 is derived: the peak voltage at output increases when the sensor is brought closer to an object. To test this AT01, which is to test the voltage at the output when the sensor is moved closer to an object, is suggested because if the acceptance test is passed, R01 is complete and the system does ’sense’/respond to when an object is in front and by the sides of the micromouse.

### 2.4.2 Traceability Analysis 2

From R02, which is that the output of the system shall be consistent at different distances from an object, SP02, SP03 and SP04 can be derived. SP02 specifies that the peak output voltage when the sensor is 8 cm away from an object shall be greater than 2.5V with a range/consistency less than 0.2V. SP03 states that the peak output voltage when the sensor is 16 cm away from an object shall be within 0.9V and 1.7V with a range/consistency less than 0.2V. SP04 states that when no object is sensed, the voltage at the output shall be less than 0.5V with a range/consistency less than 0.2V and the output trace shall have an amplitude less than 0.1V. These specifications can be tested through AT02, AT03 and AT04: measuring the output voltages when the sensor is 8 cms, 16cm and appropriately far away from an object, respectively. If all these tests are passed, the output of the system shall be deemed consistent at different distances from an object.

### 2.4.3 Traceability Analysis 3

R03 is that the outputs of system shall be suitable for the microcontroller. From this SP05 is derived: the output of the sensors shall never be more than 3.3V. To complete this, AT04 is conducted to measure the voltage regulator’s

2.4. Traceability Analysis

output voltages w.r.t. ground. This is because the sensors cannot output more than their input voltage, which should be equal to 3.3V.

### 2.4.4 Traceability Analysis 4

R04 states that the system shall be power efficient when in operation and have mitigation means on the effects of ambient light on the system. This results in SP06: which is that the emitter/sender of sensor shall be pulsed at a particular pulse width and duty cycle. This can be tested through AT06, which is by measuring the pulse length and duty cycle, ensuring that the emitter/sender is pulsed, thereby saving power when in operation.

### 2.4.5 Traceability Analysis 5

From R05, being that the components on the PCB shall be accessible to be tested, SP07 can be derived: test points shall be placed across key components in order to measure their voltage w.r.t. ground, because this allows the components to be tested. This can be approved through AT07 in that each test point on PCB shall be tested to ensure that they are working correctly.

### 2.4.6 Traceability Analysis 6

R06 states that the total cost of PCB shall be within the budget. This results in SP08 stating that the total cost of two PCB boards shall be no more than 30 USD. This can be evaluated through AT08, which is by calculating or determining the price of two boards.

### 2.4.7 Traceability Analysis 7

R07 is the power shall be supplied by a battery from which SP09 can be derived: a polymer lithium ion battery rated at 3.7V and 800mAh. To test this AT09 is suggested, which is to measure the voltage across the battery, ensuring that the battery is operating as expected.

### 2.4.8 Traceability Analysis 8

R08 states that the PCB shall be small enough and be shaped such that the micromouse can fit in the pathways and turn through corners of the maze. This leads to SP10, which specifies that the maximum length and width of the PCB shall be smaller than 60mm because a PCB smaller this shall fit in the pathways and turn through corners of the maze. This can be tested through AT09: measuring the dimensions of the PCB.

### 2.4.9 Traceability Analysis 9

From R10, PCB shall not be too heavy, SP12 can be derived. This is that the mass of the PCB shall not be more than 300g as this will cause the centre of mass of the micromouse to change dramatically making it difficult for it to turn and could cause the micromouse to topple. SP12 can be evaluated through AT12, where the mass of PCB is measured.

# Chapter 3

# Subsystem Design

## 3.1 Design Decisions

The battery that is supplying power to the micromouse is a Polymer Lithium Ion battery rated at 3.7V and 800mAh. It provides a voltage that ranges from 3.75V to 4.2V. This difference would cause a change in the output of the system at the same distance at two different instances in time, hence reducing the consistency. A voltage regulator is needed so that a fixed voltage is supplied irrespective of the change of the batteries voltage. The voltage regulator shall output 3.3V to the sensor subsystem and be a basic component supplied by the PCB manufacture as it reduces the cost of the component significantly. Three voltage regulators were considered:

Table 3.1: Voltage regulators

Voltage Regulator | Price ($) | Accuracy (±%) | Quiescent Current (mA) | I_out_max (mA)
HT7533-1 | 0.097 | 3 | 0.0025 | 100
XC6206P332MR | 0.092 | 2 | 0.001 | 200
AMS1117-3.3 | 0.127 | 3 | 5 | 1000

The parameters considered in determining the correct voltage regulator were the price, accuracy, quiescent current and the maximum output current of the voltage regulator. The quiescent current indicates the power consumption, and ideally, this value should be as low as possible. Herewith, the XC6206P332MR is chosen as it has the greatest accuracy, the lowest price and the lowest quiescent current (power-consumption) of the three voltage regulators. Its maximum output current is also the most suitable as the current draw of the sensor subsystem will be lower than 200mA.

Due to the limitation of a strict budget and size, simplicity should be a central goal of the sensor subsystem. The complexity and sophistication of the sensor should be relevant only to the amount of information that needs to be received or transmitted. Adding too many sensors or using too complicated of sensors will not necessarily improve the performance or functionality of the micromouse. Therefore, the minimum of three sensors would be placed in the front and sides of the sensor board to detect objects and barriers on the sides and in front of the micromouse aligning with SP01. Multiple sensor systems were also considered. A touch sensor acts operates like a switch when touched or pressed against an object. A sonar sensor emits ultrasonic waves and converts the reflected waves from the object into a signal, thereby indicating the distance the object is from the sensor. An infrared sensor emits a specific frequency of infrared radiation (IR) to an object, and uses the amount of reflected IR to generate a signal, thereby also determining distance. Table 3.2 below shows the pros and cons of these sensors.

Table 3.2: Pro’s and con’s of various sensor systems

Sensor
System
Pros | Cons
Sonar | • Not affected by colour or reflectiveness of
object
- Not affected by ambient light
- Most accurate
- Generates an analogue signal
- Material reflect and absorb sound differently
- Not good at defining the edges of a corner
- Expensive
Touch | • Output signal is most accurate • Cost-effective • Power and energy-effective
- Only two logic outputs: one when it has touched the wall and one when it has not
- Not time-efficient as bumping into walls will increase time taken to finish the maze
- Requires that the microcontroller not move too fast through the maze as to not damage any of its components when it bumps into a wall

3.1. Design Decisions

Sensor
System
Pros | Cons
Infrared | • Cost-effective
- Power and energy-effective
- Generates an analogue signal
- Sensitive to ambient light

The infrared sensor is the most logical choice as it provides a cost and power-effective solution whilst meeting the requirements of the sensor subsystem. One major con of the infrared sensor is that it is sensitive to ambient light. However, if the IR emitter is pulsed, the affects of ambient light can be mitigated by comparing the IR receiver output when the emitter is on and when it is off. Pulsing the emitter also saves power, which is needed to keep the battery from dying for longer.

The IR receiver must have a fast response time to perform cohesively with the pulsing of the IR emitter. Therefore, the phototransistor is a better choice for the receiver as it has a faster response time than that of a photodiode.

To narrow down the selection for the IR emitter and receiver, the pair shall operate at the same peak wave length and be 5mm radially sized (as they can be bent to face horizontally and generally fit well on the board). The IR emitter shall have a high radiant intensity, a low forward voltage and be suitable for high pulse current operation. The following IR emitters are the most appropriate in terms of the above parameters from their respective manufacturers and have stocks above 1000 on the PCB manufacturer.

Table 3.3: IR emitters

Emitter | Price ($) | Forward Voltage (V) | Peak Wave-length (nm) | Radiant Intensity | Viewing Angle (◦ )
IR204/H60 | 0.055 | 1.4 | 940 | 35mW/sr@100mA | 50
TSAL6400 | 0.164 | 1.35 | 940 | 50mW/sr@100mA | 25
MHL512IR059CRT | 0.083 | 1.35 | 940 | 3mW/sr@20mA | 70
DY-FIR333C/H34-A5 | 0.054 | 1.3 | 940 | 85mW/sr@100mA | 10

Initially, the DY-FIR333C/H34-A5 seems to be the most favourable pick. However, its viewing angle, 10◦
is too small
(and the IR204/H60 and the MHL512IR059CRT is far too big) . If the emitter were to be moved in any way, it may cause the sensor to underperform. Therefore to be conservative, the TSAL6400 is chosen with a viewing angle of 25◦ .
Although the TSAL6400 is the most expensive, the budget is somewhat disregarded as the sensor is the most crucial part of the subsystem.

For the phototransistor, the parameters considered are the saturated collector-emitter voltage and the photo sensitivity. The following phototransistors in Table 3.4 are the most appropriate in terms of the above parameters from their respective manufacturers, have stocks above 1000 on the PCB manufacturer and have a peak wavelength of 940nm. PT333-3B is chosen as it provides the greatest difference in collector current for a change in irradiance, meaning it is

Table 3.4: Phototransistors

Receiver | Price ($) | VCEsat (V) | On State Collector Current (mA) @ Ee = 1mW/cm² | On State Collector Current (mA) @ Ee = 0.5mW/cm²
MHL524PT03BRT | 0.089 | 0.4 | 1.4 | 0.5
PT204-6B-27 | 0.064 | 0.4 | 1.9 | 0.9
PT333-3B | 0.048 | 0.4 | 6.4 | 1.0
TEFT4300 | 0.209 | 0.3 | 3.2 | 1.2

the most light-sensitive. It is also the cheapest option. The saturated collector-emitter voltage is ignored as all of the phototransistors have a similar value.

The final design of the sensor-subsystem integrates the above chosen components along with passive components to ensure that an appropriate balance of performance, efficiency, and cost-effectiveness is achived. Power supplied by the battery is regulated by the XC6206P332MR voltage regulator to provide a constant 3.3V output for the sensor circuits which is necessary for the consistency of the sensor-subsystem. The sensor subsystem uses three infrared sensors made up of the TSAL6400 IR emitters paired with PT333-3B phototransistors to detect obstacles and navigate the maze efficiently. The shape of the PCB is rounded at the front to house the emitters and phototransistor pairs. The front

3.2. Calculations

sensor is placed in the front and middle of the PCB, and the left and right sensors are placed on the left and right of the front of the PCB respectively, facing slightly forward to anticipate turns in the maze. To reduce the effects of the IR sensors to ambient light and to extend battery life, the IR emitter circuit is designed such that the IR emitters are pulsed. Thereupon, the receiver circuit is designed in such a way as to integrate cohesively with the pulsing of the emitters. The emitter circuit includes a MOSFET to control the pulsing of the IR emitter, providing fast switching capabilities and low power consumption.

## 3.2 Calculations

### 3.2.1 Emitter Circuit

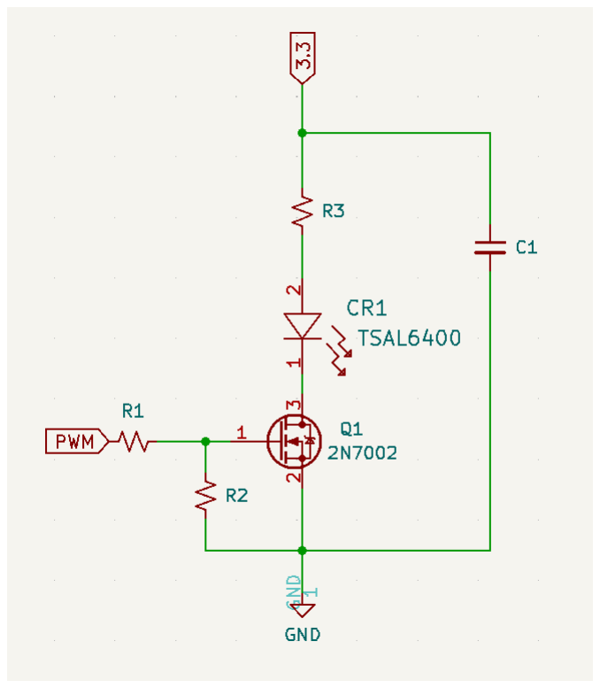
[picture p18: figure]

Figure 3.1: Emitter Circuit

R3 limits the current through the IR emitter. The desired current running through the emitter is 20mA.

Vdrop = 3.3V − VCEsat = 3.3V − 1.35V = 1.95V

RDSOn of MOSFET is small and can therefore be neglected.

∴ R3 = 1.95V /20mA = 97.5Ω ≈ 100Ω

R1 limits current flow from the microcontroller to the mosfet gate.

R1 = 100Ω

R2 is a pull-down resistor. It pulls the MOSFET gate low, thereby keeping the emitter off when the microcontroller pin is floating or disconnected. It is a high resistance to not draw too much current.
R2 = 47kΩ

C1 stabilizes the supply voltage from the switching noise and also reduces the turn on time for the IR emitter.

C1 is a 4.7uF and a 0.1uF capacitor in parallel.

The 4.7uF capacitor smooths out the voltage whereas the 0.1uF capacitor will act as a high frequency noise filter. *The 2N7002 is chosen for the MOSFET as it is the only basic MOSFET suited for low-voltage, low-current application with fast-switching speeds that is supplied by the manufacturer.

### 3.2.2 Receiver Circuit

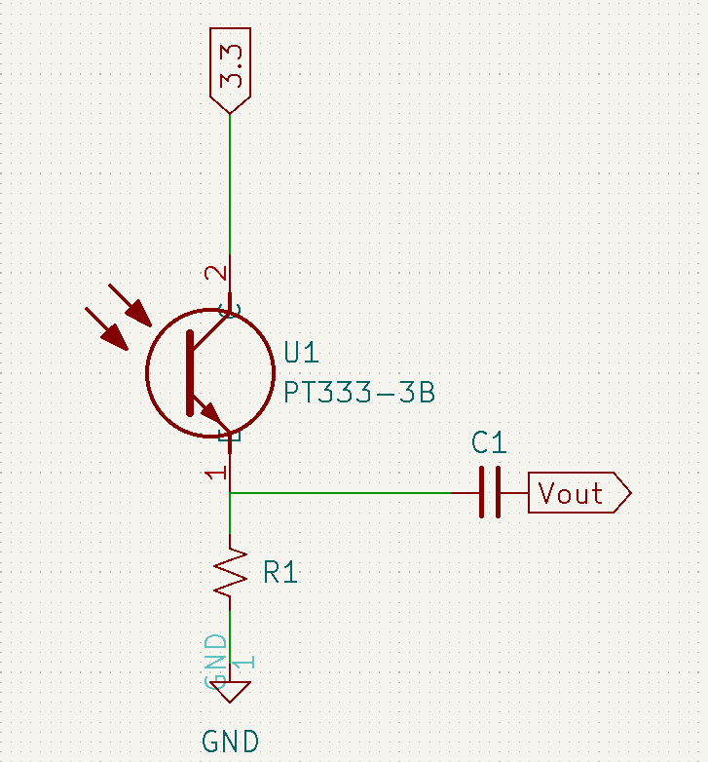
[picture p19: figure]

Figure 3.2: Receiver Circuit

The more light that is received from the emitter by the phototransistor, the more current that flows through the phototransistor.

Since the input of the analogue pins of the microcontroller have high impedance, resistor R1 creates a voltage divider. The output voltage is across R1. R1 must be chosen such as to maximise the resolution of the sensor and to also limit the current through the circuit. Increasing the resistance causes more voltage to drop across the output for the same changes in current.

Vout = R1 ∗ I

Therefore, increasing the resistance makes the output more sensitive to light. Because it is difficult to know how much light will be exposed to the phototransistor, R1 has been chosen to be a fixed resistor in series with a variable resistor.

R1 = Rpot + Rf ixed

The minimum resistance of R1 will be equal to Rf ixed, whilst the variable resistor can increase from this to a maximum of R1 = Rpotmax + Rf ixed.
Let the maximum current Imax = 3mA. Using KVL:

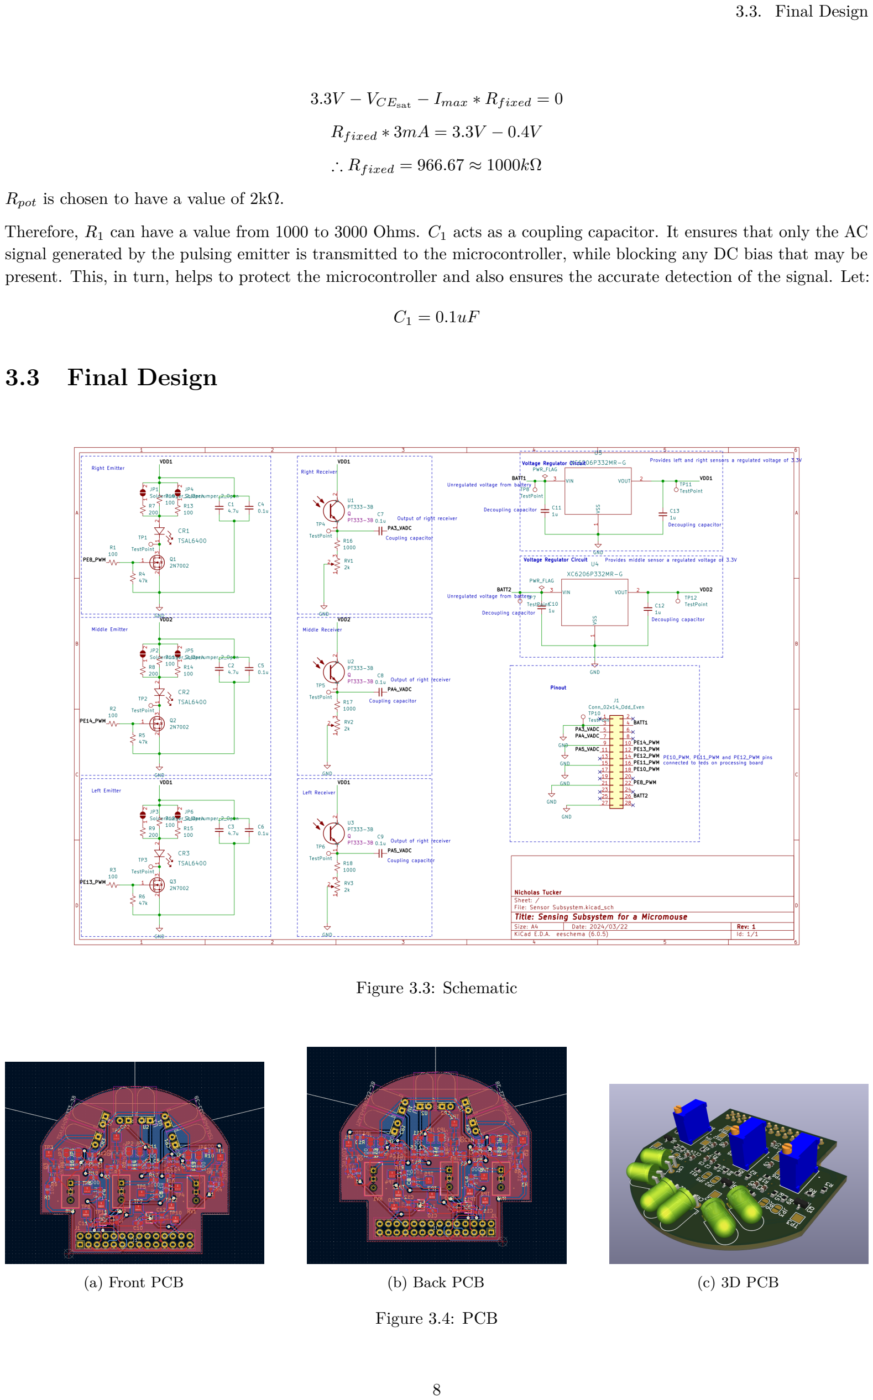
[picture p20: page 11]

3.3. Final Design

3.3V − VCEsat − Imax ∗ Rf ixed = 0

Rf ixed ∗ 3mA = 3.3V − 0.4V

∴ Rf ixed = 966.67 ≈ 1000kΩ

Rpot is chosen to have a value of 2kΩ.

Therefore, R1 can have a value from 1000 to 3000 Ohms. C1 acts as a coupling capacitor. It ensures that only the AC signal generated by the pulsing emitter is transmitted to the microcontroller, while blocking any DC bias that may be present. This, in turn, helps to protect the microcontroller and also ensures the accurate detection of the signal. Let:

C1 = 0.1uF

## 3.3 Final Design

Figure 3.3: Schematic

(a) Front PCB | (b) Back PCB | (c) 3D PCB

Figure 3.4: PCB

3.4. Failure Management

## 3.4 Failure Management

Table 3.5 shows the failure management processes in regards to the PCB design and why they are implimented:

Table 3.5: The failure management processes taken

Name | Description
Solder jumpers placed in parallel with resistor that is in series with IR emitter of the emitter circuit. | If too little current is flowing into the IR emitter such that the radiant intensity of the emitter under performs, the jumper can be soldered to bridge the gap. This, thereby, reduces the equivalent resistance of the branch causing more current to flow and in- creasing the radiant intensity of the IR emitter. The equivalent resistance can therefore have values of 100, 67, 50 or 40 Ohms.
Potentiometer placed in series with resistor across phototransistor of receiver circuit. | The potentiometer is connected as a variable resis- tor. Its resistance can range from 0 to 2000 Ohms. Because a 1k Ohm resistor is placed in series with it, the combined resistance can range from 1k to 3k Ohms. Increasing the resistance causes more voltage to drop across the output for the same changes in current. Therefore, increasing the resistance of the potentiometer makes the output more sensitive to light. If there is too little change in the output when an object is sensed, the resistance of the potentiome- ter can be increased to counteract this.
Jumper test points placed before or after key compo- nents. | The voltage before or after (depending on where the test point is placed) can be measured w.r.t. ground. Hence, if a problem were too occur within the subsys- tem circuitry, the problem can be isolated with much greater precision than if no test points were placed. The problem can then be identified and solved for.

## 3.5 System Integration and Interfacing

Table 3.6 shows which pins connect to and interact with other parts of the system:

Table 3.6: Interfacing specifications

Interface | Description | Pins/Output
I01 | Sensor outputs to STM for data transfer
- Output of right receiver to analogue input STM PA3
- Output of middle receiver to analogue input STM PA4
- Output of left receiver to analogue input STM PA5
- GND: right, middle and left emitter and receiver GNDs to STM GND
I02 | STM to sensor subsystem to pulse IR emitters of sensor subsystem
- STM PE8 (PWM) to gate resistor of 2N7002 mosfet of right emitter
- STM PE14 (PWM) to gate resistor of 2N7002 mosfet of middle emitter
- STM PE15 (PWM) to gate resistor of 2N7002 mosfet of left emitter
I03 | Battery supply to sensor subsys- tem
- BATT1 (BATT) to input of voltage regulator U5
- BATT2 (BATT) to input of voltage regulator U4
IO4 | STM (PWM) to LEDS on proces- sor board
- STM PE10 to right LED
- STM PE11 to middle LED
- STM PE12 to left LED

3.5. System Integration and Interfacing

Figure 3.5 shows a high level block diagram showing how the sensing subsystem fits into the larger system:

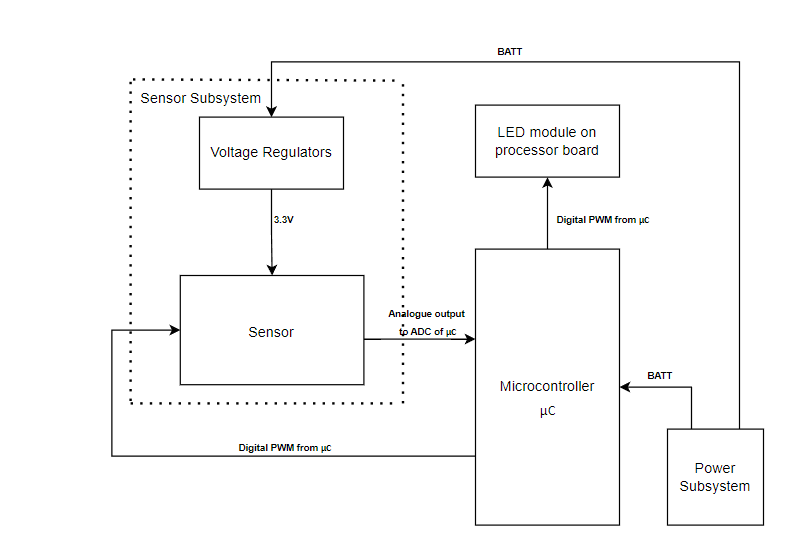
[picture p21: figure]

Figure 3.5: Interface diagram

# Chapter 4

# Acceptance Testing

## 4.1 Tests

*Assume when sensors are tested, power is supplied to the sensor subsystem, specifically to BATT1 and BATT2, which connect to the input of the voltage regulators U5 and U4 respectively. The emitters are also pulsed using PWM provided by the microcontroller to the gate resistors of the mosfets of the emitter circuits. Assume also that each sensor (right, left and middle) are tested independently. These are test points TP4, TP5 and TP6, which are the test points at the output of the right, left and middle receiver respectively.

Table 4.1: Sensor subsystem acceptance tests

Test
ID | Description | Testing Procedure | Pass/Fail Criteria

AT01

Voltage at output shall be tested when sensor is moved closer to an object.

- Oscilloscope is connected to the test point at the output of the receiver and to the ground test point TP10.
- The sensor is placed a distance away from a barrier and slowly brought closer (perpendicular) to the barrier until it is approximately 5cm away.
- Whilst the sensor is moved, the waveform of the output voltage on the oscilloscope is observed.

PASS: the peak voltage increases and the minimum/low voltage remains the same with an acceptable range of ±0.03V as the sensor moves towards the barrier.
FAIL: the peak voltage stays the same or decreases as the sensor moves towards the barrier.

AT02

Output voltage when sensor is 8 cms away from an object shall be measured.

- Oscilloscope is connected to the test point at the output of the receiver and to the ground test point TP10.
- Using a ruler or tape-measure, the sensor is placed 8cm perpendicular to a barrier.
- The peak voltage is measured using the oscilloscope.
- The test is repeated at least five times with the sensor being turned off for at least 10 seconds and then turned on, then moving the sensor back and forwards to the 8cm mark each time and each peak voltage measurement is recorded.

PASS: the average of the peak output voltages is greater than 2.5V and the range is less than ±0.2V. If the range of these voltages is less than ±0.2V but average less than 2.5V, the radiant intensity of the emitters must be adjusted until the voltages average greater than 2.5V. FAIL: the voltages are inconsistent. The peak voltage range is greater than ±0.2V. The radiant intensity of the emitter cannot be adjusted such that the voltages are greater than 2.5V.

4.1. Tests

Test
ID | Description | Testing Procedure | Pass/Fail Criteria

AT03

Output voltage when sensor is 16cm away from an object shall be measured.

- Oscilloscope is connected to the test point at the output of the receiver and to the ground test point TP10.
- Using a ruler or tape-measure, the sensor is placed 16cm perpendicular to a barrier.
- The peak voltage is measured using the oscilloscope.
- The test is repeated at least five times with the sensor being turned off for at least 10 seconds and then turned on, then moving the sensor back and forwards to the 16cm mark each time and each peak voltage measurement is recorded.

PASS: the average of the peak output voltages is between 0.9V and 1.7V and has a range/consistency less than ±0.2V.
FAIL: The average of the peak voltage is outside of 0.9V and 1.7V or the range of the peak voltages is greater than ±0.2V.

AT04

Output voltage when no object is sensed shall be measured.

- Oscilloscope is connected to the test point at the output of the receiver and to the ground test point TP10.
- Ensure that no barrier/object is within 3m to the front of the sensor.
- The voltage is measured using the oscilloscope.
- The test is repeated at least five times with the sensor switched off for at least 10 seconds and on each time and each voltage measurement is recorded.

PASS: The voltages lie within a range of ±0.2V and average less than 0.5V. The waveform of the output voltage must also be flat with a maximum amplitude of 0.1V. FAIL: Voltages lie outside a range of ±0.2V or the average of the voltage measurements is greater than 0.5V. FAIL: Amplitude of output voltage trace is greater than 0.1V

AT05

Voltage regulator’s output voltages shall be measured w.r.t. ground.

- Oscilloscope is connected to the output of each voltage regulator, TP11 and TP12, and to the ground test point TP10.
PASS: | Voltage | is | equal | to
(3.3±0.02)V
FAIL: Voltage is not equal to (3.3±0.02)V

AT06

Pulse length and duty cycle of emitter and receiver shall be measured.

- Oscilloscope is connected to the test point at the drain of the MOS-FET (TP1, TP2 and TP3) and to the ground test point TP10. Measure the pulse length and calculate the duty cycle using the oscilloscope.
- Using a ruler or tape measure, position the sensor 1cm away from a barrier and connect the oscilloscope to the test point at the output of the receiver and to the ground test point TP10. Measure the pulse length and calculate the duty cycle using the oscilloscope.

PASS: the measured pulse length and duty cycle of both the receiver and emitter match the input pulse signal, with a maximum deviation of 5% for each.
FAIL: The measured pulse length or duty cycle of either the receiver or emitter deviates from the input pulse signal by more than 5%.

AT07

Each test point on PCB shall be tested to ensure they are working correctly.

- Ensure power is supplied normally to the sensor subsystem, with emitters being pulsed.
- Multimeter is set on the continuity test mode
- Multimeter is then systematically connected to every test point that is not the ground test point and the ground test point.

PASS: Every test point passes the continuity test.
FAIL: At least one test point fails the continuity test.

AT08 Total cost of PCB shall be calculated.

- Price of PCB can be found on quote from PCB manufacturer.

PASS: Cost of 2 PCB’s is less than 30 USD
FAIL: Cost of 2 PCB’s is more than 30 USD

4.2. Critical Analysis of Testing

Test
ID | Description | Testing Procedure | Pass/Fail Criteria
AT09 | Voltage across battery shall be measured.
- Using a multimeter, connect one probe to TP8, which is connected to the BATT1 pin, and connect the other probe to the ground test point, TP10.
- Using a multimeter, connect one probe to TP7, which is connected to the BATT12 pin, and connect the other probe to the ground test point, TP10.

PASS: both voltages measured lie within the range 3.75 to 4.2V. FAIL: at least one of the voltages lie outside of this range.

AT10 The dimensions of the PCB shall be measured.

- Using a ruler or tape measure, the maximum width and length of the PCB is measured.

PASS: the maximum length and width are both smaller than 60mm. FAIL: the maximum length or width is greater than 60mm.

AT11 Mass of PCB shall be mea- sured.

- Using a scale, mass of PCB is measured. The manufacturer may also provide a calculated mass.

PASS: the mass is less than 300 grams.
FAIL: mass is equal to or greater than 300 grams.

## 4.2 Critical Analysis of Testing

Table 4.2: Subsystem acceptance test results

Test
ID | Description | Result
AT01 | Voltage at output shall be tested when
| sensor is moved closer to an object. | PASS
AT02 | Output voltage when sensor is 8 cms
| away from an object shall be measured. | FAIL
AT03 | Output voltage when sensor is 16cm
| away from an object shall be measured. | FAIL
AT04 | Output Voltage when no object is sensed
| shall be measured. | PASS
AT05 | Voltage regulator’s output voltages shall
| be measured w.r.t. ground. | PASS
AT06 | Pulse length and duty cycle of emitter
| and receiver shall be measured. | PASS
AT07 | Each test point on PCB shall be tested
| to ensure they are working correctly. | PASS
AT08 | Total cost of PCB shall be calculated. | PASS
AT09 | Voltage across battery shall be mea-
| sured. | PASS
AT10 | The dimensions of the PCB shall be
| measured. | PASS
AT11 | Mass of PCB shall be measured. | PASS

The five most significant ATPs are discussed and assessed below:

### 4.2.1 AT01

Figure 4.1 below show the outputs of the front sensor when the PCB is slowly brought closer (perpendicular) to the barrier at three different instances:

4.2. Critical Analysis of Testing

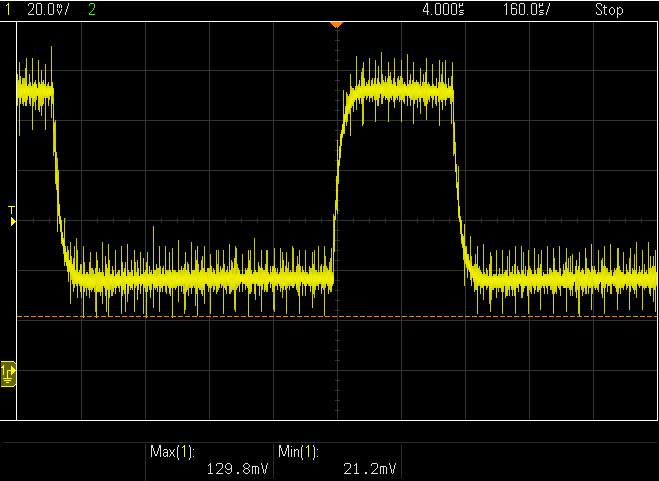
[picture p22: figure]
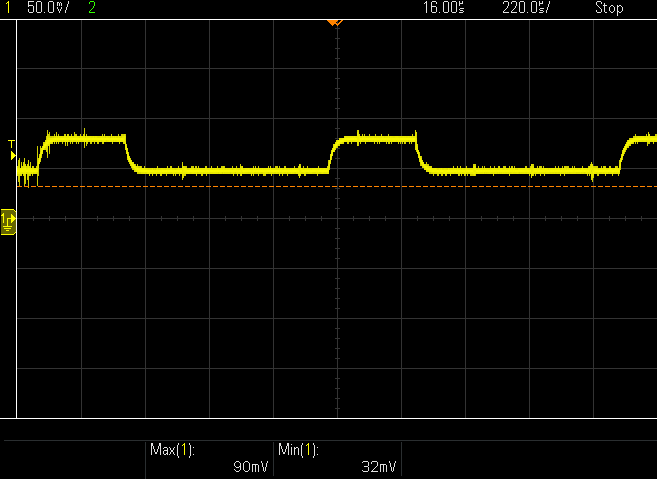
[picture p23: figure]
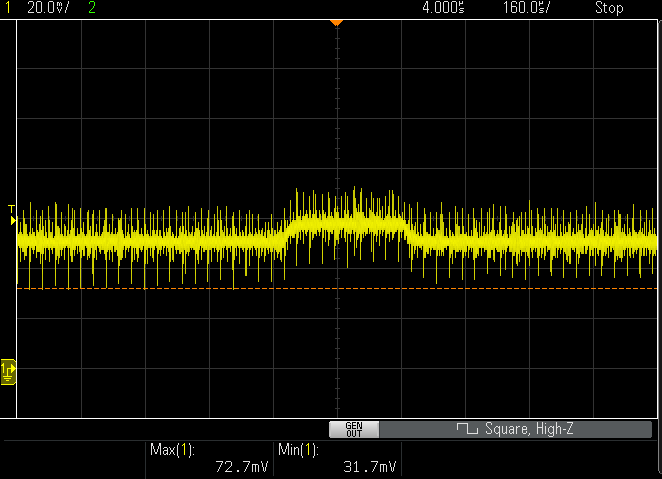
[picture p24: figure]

(a) Far | (b) Medium | (c) Near

Figure 4.1

The peak voltage clearly increases from left to right, where the maximum voltage is equal to 72.7mV when the PCB is far from the wall, 90mV when the PCB is at a medium distance from the wall and 129.8mV when the PCB is placed flush against the wall. The minimum/low voltage levels are equal to 31.7mV when the PCB is far from the wall, 32mV when the PCB is at a medium distance from the wall and 21.2mV when the PCB is placed flush against the wall. The left and right sensor outputted essentially identical results and thus for the brevity of this section, only outputs from the middle sensor are shown. Nonetheless, a considerable amount of noise can be observed in the waveforms on the oscilloscope. Because of this, these measurements are not necessarily precise and accurate and may affect the quality of information transferred to the microcontroller. However, the test only considers how the peak voltage changes as the PCB is moved relative to a barrier and the amount the minimum/low voltage changes. Since the peak voltage increases as the sensor moves towards the barrier and the most the minimum/low voltage changes is less than 0.03V, AT01 is passed.

### 4.2.2 AT02

In order for ATP02 to be passed the peak output voltage must be greater than 2.5V and the range less than ±0.2V. If the range of these voltages is less than ±0.2V but average less than 2.5V, the radiant intensity of the emitters must be adjusted until the voltages average greater than 2.5V. Initially, the peak voltages were indistinguishable, and no pulses could be seen in the output of the sensor. To solve this, failure management processes are used: the solder jumpers placed in parallel with resistor that is in series with IR emitter of the emitter circuit were soldered to increase the radiant intensity of the emitters. The resistance of the potentiometer of the receiver circuit was also maximised, such that the receiver circuit was the most sensitive to light it could be, and create larger voltage changes in the pulses of the output of the sensor. Figure 4.2 below shows the output of the middle sensor when the PCB is placed 8 cm perpendicular to a barrier with the failure management processes taken:


Figure 4.2: Output voltage when sensor is 8 cms away from wall

The peak voltage of the sensor is equal to 90.7mV and the minimum voltage (the voltage when the IR emitters are off when pulsing) is equal to 34.4mV. However, the peak voltage of the sensor remains consistent, and keeps within a

4.2. Critical Analysis of Testing

range of ±20mV when turned on and off multiple times and moved around. Thus, the consistency condition of AT02 is satisfied. However, ultimately since the peak output voltages were much less than 2.5V, AT02 is failed.

Since the test is failed so substantially, and all failure management processes have already been taken as to meet the pass conditions for the acceptance test, the potentiometer (RV1, RV2 and RV3) is removed. Through a process of trial-and-error, a 1MΩ is chosen to replace the potentiometer. This is done because even when the resistance of the potentiometer is set at its maximum value and the resistance in series with the phototransistor is then 3kΩ. The resistance is still far too small to draw a significant voltage difference between when the emitters are pulsed off and then on. Figure 4.3 shows the output of the middle sensor when the PCB is placed 8 cm perpendicular to a barrier and the potentiometer is replaced by a 1MΩ resistor. The left and right sensor display essentially the same result:


Figure 4.3: Output voltage when sensor is 8 cms away from wall and potentiometer is replaced by a 1MΩ resistor

The peak voltage of the sensor is now higher with a value of 973mV, which is more than ten times the peak voltage of the sensor before. Comparing the two waveforms, the noise also reduces considerably. Again the peak voltage of the sensor remains consistent, and keeps within a range of ±20mV when turned on and off multiple times and moved around, and thereby still satisfies the consistency condition of AT02. Nonetheless, since the peak output voltage is still less than 2.5V, AT02 is failed. However, a significant improvement to the design is made. The reason why the peak output voltage is still too low is because the 0.1uF capacitor (C7, C8, and C9) connecting the output of the sensor to the microcontroller may be causing a significant voltage drop to the output voltage. Therefore, to fix this problem, a larger capacitor can be used such as 0.5uF, or the frequency of the input PWM to the emitter circuit can be increased. If neither of these options work, the capacitors (C7, C8, and C9) can be short-circuited.

### 4.2.3 AT04

In order for AT04 to be passed, when no barrier is placed in front of the sensor, the output voltage must lie within a range of ±0.2V and average less than 0.5V. The trace of the output voltage must also be flat with a maximum amplitude of 0.1V. Figure 4.4 shows the output of the middle sensor under the testing conditions. The left and right sensor display very similar results. The potentiometer is set at is maximum resistance and the emitters operating at their full radiant intensity:

4.2. Critical Analysis of Testing


Figure 4.4: Output voltage when no barrier is placed in front of the sensor

The output lies far below 0.5V and the waveform is flat with an amplitude of approximately 40mV. The output voltage also stays within a range of ±0.1V when the sensor is turned on and off and moved around. Therefore, AT04 is passed as it passes all the conditions. Observing the waveform of figure 4.4, a lot of noise is present. This reduces the quality of the information passed on to the microcontroller. The noise is a result of the resistance in series with the phototransistor of the receiver being too low, causing the output voltage to be lower and thus being more susceptible to noise. Figure 4.5 below shows the output of the middle sensor when no barrier is placed in front of it, and the potentiometer is replaced by a 1MΩ resistor. Once again, the left and right sensor display essentially the same results:


Figure 4.5: Output voltage when no barrier is placed in front of the sensor and potentiometer is replaced by a 1MΩ resistor

Although the output voltage still stays within a range of ±0.1V when the sensor is turned on and off and moved around, the output lies just above 0.5V and the waveform is no longer flat. Therefore, AT04 fails. However, replacing the potentiometer with a 1MΩ resistor is imperative to use the resolution of the ADC more effectively, thereby creating a more functional sensor subsystem. The effect of noise is also reduced as a result. The reasoning behind pulses being observed in the output voltage even though no barrier is placed in front of the sensor is because the receiver is slightly detecting the pulses of the emitter adjacent to it (due to the IR of the emitter being detectable in the viewing angle of the phototransistor). Hence, to fix this, insulating tape can be wrapped around the phototransistor leaving only the front of it exposed, thereby reducing the viewing angle, causing the waveform to be more flatter.

### 4.2.4 AT05

Voltage regulator’s (U5 and U4) output voltages (VDD1 and VDD2) is measured w.r.t. ground. Figure 4.6 below shows the measurement for both voltage regulators measured using a multimeter:

4.2. Critical Analysis of Testing


(a) Vout of U5 (Vdd1) | (b) Vout of U4 (Vdd2)

Figure 4.6: Measurement for both voltage regulators using a multimeter

The output of both voltage regulators is within the range of (3.3±0.02)V. Therefore, AT05 is passed. This ensures that the voltage at the output of the sensors will hence never be larger than 3.3V thereby protecting the internal circuitry of the microcontroller and ensuring that the change in the output of the system at the same distance at two different instances in time is constant.

### 4.2.5 AT06

Pulse length and duty cycle of emitter and receiver is measured. The input PWM signal has a frequency of 1kHz and a duty cycle of 30%. Therefore, the pulse length for the input PWM signal is 0.3ms. The measured signal at the front emitter matches the input pulse signal with a pulse length of exactly 0.3ms and 30% duty cycle. Figure 4.7 shows the output of the middle sensor when it is 1cm away from a barrier. The potentiometer is set at is maximum resistance and the emitters operating at their full radiant intensity. The left and right sensor display the same results.


Figure 4.7: The output of the middle sensor when it is 1cm away from a barrier

The pulse length is measured to be 0.32ms and the period is measured to be 1.04ms. Therefore, the duty cycle is calculated to be 31%. AT06 is passed as the measured pulse length and duty cycle of both the receiver and emitter match the input pulse signal, with a maximum deviation of within 5% for each.

Figure 4.8 below shows the output of the middle sensor when it is 1cm away from a barrier, and the potentiometer is replaced by a 1MΩ resistor. Once again, the left and right sensor display essentially the same results:

4.2. Critical Analysis of Testing


Figure 4.8: The output of the middle sensor when it is 1cm away from a barrier and the potentiometer is replaced by a 1MΩ resistor

The pulse length is measured to be 3ms and the period is measured to be 1ms. Therefore, the duty cycle is calculated to be 30% and thus AT06 is passed.

# Chapter 5

# Conclusion

This report is aimed to design, develop and test the hardware for the sensor subsystem of a micromouse. The sensing subsystem uses and integrates with the already designed processor, motherboard, and power subsystem in order for the micromouse to successfully traverse through a maze. The sensor subsystem ensures that the micromouse can detect obstacles and maintain proper alignment within the pathways of the maze. The report outlines the specific objectives and goals of the sensing subsystem. It identifies the requirements and specifications for the subsystem, discusses the decisions involving component selection, evaluates possible solutions and provides calculations used to design the sensing subsystem. It also details the testing procedures used to evaluate if the specification of the subsystem are met. Additionally, it addresses design considerations for mitigating failure in the sensing subsystem circuit design and demonstrates how the subsystem fits into the larger micromouse system.

To summarize some of the significant acceptance tests, the output voltages of the voltage regulators are within the acceptable range, thereby protecting the internal circuitry of the microcontroller and keeping the output of the system at the same distance, at two different instances in time, constant (AT05). The measured pulse length and duty cycle of both the emitter and receiver also matched the input pulse signal within a maximum deviation of 5%, confirming the switching capabilities of the emitter circuit and the receiver circuit. However, though most of the acceptance tests, AT01, AT04, and AT05 to AT11 were passed, there are some problems with the final design of the sensor subsystem. Through the critical analysis of the acceptance tests where the output of the sensors were directly assessed (AT01 to AT04), a major problem is that the peak output voltage increases to a much smaller than accepted degree when the sensor moves closer to a barrier (not sensitive enough to changes in proximity of the sensor to the barrier). This is why tests AT02 and AT03 were failed. Therefore, the output of the sensor is not fully maximized for the ADC of the microcontroller. However, suggestions were made to resolve this problem. These include replacing the potentiometer with a 1MΩ resistor, which significantly improved the sensitivity (and reduced noise present in the output waveform) of the receiver circuit. Suggestions such as increasing the frequency of the PWM signal to the emitter circuit or increasing the capacitance of the coupling capacitors that connect the output of the sensor to the microcontroller were also suggested but were not tested. Nontheless, the peak output voltage increased enough as to provide the microcontroller with enough information as to tell if a barrier was placed, to the left, right and front of it, thereby making it capable for the micromouse to successfully traverse through the maze with proper alignment within the pathways of the maze.

The project faced several challenges, including a limited budget and time frame, which restricted component selection and the depth of design iterations and testing. Despite having access to basic lab equipment, the lack of specialized facilities may have constrained the range and quality of tests conducted. Therefore, the design of the sensor-subsystem is by no means perfected and recommendations can be made.

## 5.1 Recommendations

The 1kΩ resistor in series with the 2kΩ potentiometer in each receiver circuit should be replaced by a much larger resistance, such as a 500kΩ resistor in series with a 1MΩ potentiometer. This increases the sensitivity of the reciever circuit drastically while also being able to control it. The coupling capacitors that connect the sensors outputs to the microcontroller can also be replaced by a larger capacitance, such as 0.5uF capacitors. The effects of the frequency of the PWM on the output of the sensor should also be fully understood to achieve the most efficient match. Filters such as band pass filters could also be placed where output of the sensor connects to the analogue pins of the microcontroller to reduce noise in the sensor output, thereby improving the sensor’s accuracy. Insulating tape should also be placed around each phototransistor of the receiving circuits to reduce the viewing angle of the sensor. This helps to prevent the sensor from detecting the infrared (IR) pulses emitted by the adjacent emitters. If all these changes are implimented, a significant improvement to the design can be achieved.

# Chapter 6

# Bibliography


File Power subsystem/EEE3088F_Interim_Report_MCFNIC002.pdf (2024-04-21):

# Interim Design Report

Micromouse Power Subsystem


Prepared by:
Nicholas McFarland
MCFNIC002

Prepared for:
EEE3088F
Department of Electrical Engineering University of Cape Town

April 21, 2024

# Declaration

1. I know that plagiarism is wrong. Plagiarism is to use another’s work and pretend that it is one’s own.
2. I have used the IEEE convention for citation and referencing. Each contribution to, and quotation in, this report from the work(s) of other people has been attributed, and has been cited and

referenced.

3. This report is my own work.
4. I have not allowed, and will not allow, anyone to copy my work with the intention of passing it off as their own work or part thereof.


April 21, 2024

Nicholas McFarland | Date

ii

# Contents

1 Introduction | 1
2 Requirements Analysis | 2
3 Subsystem Design | 5
4 Acceptance Testing | 11
Bibliography | 12

iii

# Chapter 1

# Introduction

## 1.1 Problem Description

The goal of this project is to build a micromouse that is capable of solving and navigating a maze. It consists of a sensing and power subsystem, and this report gives an in-depth analysis of the designed power subsystem, which will eventually be used to drive and power the micromouse. This subsystem must be capable of driving the motors used to control the wheels of the mouse and supplying the power used to drive the rest of the system.

## 1.2 Scope and Limitations

The designed circuit board uses a singular 1S1P battery to power all parts of its system and most external subsystems of the micro-mouse. It must be able to operate 2 motors at rated current and voltage and provide an analog connection that provides information to the processor regarding the battery’s current voltage and charge state. It must be able to charge the battery from an external 5V input voltage and house an ON/OFF switch that can control the power supply to the system.

Besides the connections between the power subsystem’s pin headers and motherboard, this project provides no detail into the other subsystems of the overall micromouse. It does not provide any coding required to operate the other subsystem/s.

The shape of the PCB design must feature a tab with dimensions that prevent it from obstructing the motor connections or colliding with any of the motherboard connections. The cost of producing the board may not exceed $30 when ordered, and all components selected for designing the system must be readily available on JLCPCB [1]. Finally, the design must be suitable for testing any potential

problem points on the board and feature alternative options to prevent these problems.

## 1.3 GitHub Link

https://github.com/NichTucker/Micromouse

# Chapter 2

# Requirements Analysis

## 2.1 Requirements

The requirements for a micromouse power module are described in Table 2.1.

Table 2.1: User and functional requirements of the power subsystem.

Requirement ID | Description
SW01R | Requires switching between ON/OFF state
SW02R | When OFF, current drawn by battery < 500uA
CHRG01R | Charge the battery from an input pin
CHRG02R | Recommended discharge at 0.5C (Capacity) for battery
BATT01R | Must include JST battery connector
BATT02R | Must be powered by Battery LiPo 800mAh 3.7V (https://www.robotics.org.za/802540)
MTR01R | Powers 2 motors
ADC01R | Provides information on the battery’s current voltage and
| sense of state of charge (SoC)
PCB01R | 16 available pin headers
PCB02R | Pin connector must be proud of the board
CST01R | Cost of the board must be less than $30

## 2.2 Specifications

The specifications, refined from the requirements in Table 2.1, for the micro-mouse power module are described in Table 2.2.

2.3. Testing Procedures

Table 2.2: Specifications of the sensing subsystem derived from the requirements in Table 2.1.

Specification ID | Description
SW01S | The switch must provide 2 discreet states of output voltage,
| ranging between 0V - Battery’s Current voltage
SW02S | Quiescent currents for various components will be taken from
| the datasheet/calculated.
CHRG01S | Circuit uses an Li-Po battery charger with a 5V operating
| input voltage.
CHRG02S | Drawn current < 400mA when charging
BATT01S | JST pin connector with a pin pitch of 2mm
BATT02S | Battery will be provided by EEE3088F course
MTR01S | Circuit will use a dual bridge motor driver to power and
| operate the motors. Motors operate at 200mA each and
| 3.7V. Driver selected based on operating voltage.
ADC01S | Voltage divider circuit to provide batter’s state of charge
| (SoC), as well as ensure the maximum input voltage < 3V3
PCB01S | 2x8 pin header with 2.54mm pin pitch
PCB02S | Height of tab > 18mm and width of tab < 35mm to prevent
| collision with motors
CST01S | Starting allowance at $30, with manufacture costs of $4, As-
| sembly cost of $9.50 leaving $8.25 per board for components

## 2.3 Testing Procedures

A summary of the testing procedures [2] detailed in chapter 4 is given in Table 2.3.

Table 2.3: Testing Procedures

Testing ID | Description
AT01 | All ground connections correctly grounded
AT02 | All resistor values match the design values
AT03 | Switch turns system ON when pushed DOWN and OFF when RELEASED (personal preference)
AT04 | Switch provides discreet ON/OFF states
AT05 | Quiescent current less than maximum rated
AT06 | Voltage provided by 5V pin is indeed 5V
AT07 | Charger charges battery
AT08 | Battery draws < 400mA when charging
AT09 | Motors reach operating current
AT10 | Motors reach operating voltage
AT11 | Analog sub-circuit produces calculated voltage

2.4. Traceability Analysis

## 2.4 Traceability Analysis

The show how the requirements, specifications and testing procedures all link, Table 2.4 is provided.

Table 2.4: Requirements Traceability Matrix

# | Requirements | Specifications | Acceptance Test

1 | BATT01R,BATT02R | BATT01S,BATT02S | -

Design must use the Battery LiPo 800mAh 3.7V (https://www.robotics.org.za/802540) provided by the course to power the circuit. It must be connected to the circuit with the JST battery connector.

2 | PCB01R,PCB02R,CST01R | PCB01S,PCB02S,CST01S | -
Design’s input/output connection to the rest of the system consists of a 2x8 pin header with a

2.54mm pin pitch. In order to clear the motor, the PCB must have the headers on a tab with height > 18mm and width < 35mm, and the components on this board when combined cannot cost more than $8.25.

3 | - | - | AT01

Measure all ground connections as well as the pours to ensure the design is correctly grounded.
4 | - | - | AT02

Test all resistor values to see how they vary when compared to their calculated values. Ensure they are within their rated tolerances and note how the tolerances changed their values.
5 | SW01R,SW02R | SW01S,SW02S | AT03,AT04,AT05
Design provides a discreet ON/OFF switching between the battery’s voltage and 0V, that draws

< 500uA when in the 0V state. Test this by measuring the voltages at the BATT pins for both states of the button and measuring the current being fed by the battery when the switch is off.
6 | CHRG01R,CHRG02R | CHRG01S,CHRG02S | AT06,AT07,AT08

Design must be capable of charging the battery. Test this by providing and measuring the 5V input voltage to the 5V pins, connecting the battery, and turning the switch ON. Use a multimeter to measure the current drawn by the battery, then let it charge for > 2 hours and measure its voltage to test its charge time.
7 | MTR01R | MTR01S | AT09,AT010

Design must drive 2 motors with an input of 3.7V, providing the motors with 200mA each. Ensure this by using a multimeter to measure the voltages and currents of the motors.
8 | ADC01R | ADC01S | AT11

Design uses a voltage divider to provide a 3.3V input, which gives the state of charge of the battery. Test this with a multimeter.

# Chapter 3

# Subsystem Design

## 3.1 Design Decisions

### 3.1.1 Final Design

*From component browsing on JLCPCB it was found that the 0603 package resistors and capacitors were abundantly stocked, so

unless explicitly stated otherwise all resistors and capacitors were selected from these packages.*

Motor Driver

Due to their incredibly detailed datasheets (ratings, pin connections etc), the DRV8833 motor drivers

are the best option for driving the micro-mouse. The selection choice was made by tabulating the following potential choices from JLCPCB and choosing the most viable option:

Table 3.1: Dual bridge motor driver ICs

Possible solu-tion | Rated Supply Voltage (V) | Rated Supply Current (A) | Price per IC($) | Availability | Dimensions (mm x mm)
DRV8833PWP (https://wmsc.lcsc.com/wmsc/upload/file/pdf/v2/lcsc/2303020200_Texas-Instruments-DRV8833PWP_C1556089.pdf) | 2.7 - 10.8 | 1.5 | 1.1790 | 27 | 5 x 6
DRV8833PWPR (https://wmsc.lcsc.com/wmsc/upload/file/pdf/v2/lcsc/1810151712_Texas-Instruments-DRV8833PWPR_C50506.pdf) | 2.7 - 10.8 | 1.5 | 0.6660 | 9631 | 5 x 6
DRV8833RTYR (https://wmsc.lcsc.com/wmsc/upload/file/pdf/v2/lcsc/1810010132_Texas-Instruments-DRV8833RTYR_C154936.pdf) | 2.7 - 10.8 | 1.5 | 1.185 | 1315 | 4 x 4

from Table 3.1, the DRV8833PWPR was chosen, because of the following:

- Meets the required rated voltage and current
- Much cheaper option than option 1 and option 3
- Readily available (higher stock than 1 and 3)
- The datasheet provides a typical circuit diagram of how to implement the device

All capacitors were chosen at E24 values and added to prevent any AC noise from interfering with the motor driver circuit.

3.1. Design Decisions

Battery Management

The TP4056 ICs all have the correct rated input voltage (5V) and charge voltage (4.2V). The following

ICs were considered for the design:

Table 3.2: battery management ICs

Possible solution | JLCPCB part # | Rated Input Voltage (V) | Quietient current/Iq (uA) | Price per IC($) | Availability | Dimensions (mm x mm)
TP4056 | C725790 (https://wmsc.lcsc.com/wmsc/upload/file/pdf/v2/lcsc/2311091738_UMW-Youtai-Semiconductor-Co---Ltd--TP4056_C725790.pdf) | 4.0 - 6.5 | 35 | 0.0620 | 29409 | 4 x 5
TP4056 | C17702041 (https://wmsc.lcsc.com/wmsc/upload/file/pdf/v2/lcsc/2309121405_HXY-MOSFET-TP4056_C17702041.pdf) | 4.5 - 8.0 | 55 | 0.0587 | 10658 | 5 x 5
TP5000X-4.2-ESOP8 | C5447152 (https://wmsc.lcsc.com/wmsc/upload/file/pdf/v2/lcsc/2304251410_TOPPOWER-Nanjing-Extension-Microelectronics-TP5000X-4-2-ESOP8_C5447152.pdf) | 4.0 - 9.0 | 180 | 0.2465 | 5022 | 5 x 6

From Table 3.2, the first solution (C725790) was chosen. The reasons are as follows:

- Cheaper than option 2.
- Largest available supply.
- Smallest component (reduces PCB size).
- Lowest Iq ensures lowest possible current when mouse is active.

The charging current is controlled by the Rprog resistor. From the given equation in the datasheet:

Ibat =

Vprog

Rprog

1200

Setting Rprog at 1600 Ω ensures Ibat is (750mA) which is less than the maximum rated current (1A)

and that the resistor is of E24 value. The rest of the circuit was designed with the aid of a typical charging circuit on the datasheet of a similar IC [TP4056]. (https://dlnmh9ip6v2uc.cloudfront.net/datasheets/Prototyping/TP4056.pdf)

*The selected IC has built-in voltage regulation and protection, so this was not needed in the design

Analog Sensing

This consists of a voltage divider circuit that reduces the battery’s read voltage to a maximum of 3V3 (ADC pin’s required voltage).

Since the battery has a maximum of 4.2V, simply feeding this into the ADC pin could break it, so the divider circuit must ensure Vout ≤ 3.3V. from the equation of a voltage divider:

Vout = Vin

R7
R5 + R7

Setting R5 = 10KΩ and R7 = 33KΩ, Vout is set at 3.22V which is safely below its rated voltage. By setting these resistors to a magnitude of more than 10³
, it ensures that the current in this circuit is minuscule.

3.1. Design Decisions

Circuit Switching

To ensure that the battery is fully disconnected from the circuit, the switch is connected directly after the battery (Battery -> switch -> circuit). Some of the viable JLCPCB switches that match these

requirements are tabulated below:

Table 3.3: Possible switches available on JLCPCB

Possible solu-tion | Type | Rated Volt-age (V) | Rated Cur-rent (mA) | Price per Switch($) | Availability | Dimensions (mm x mm)
EG1224 (https://wmsc.lcsc.com/wmsc/upload/file/pdf/v2/lcsc/1912111437_E-Switch-EG1224_C273395.pdf) | Slide | 15 | 500 | 0.7695 | 70 | 7 x 12
PS-5850A-6PL (https://wmsc.lcsc.com/wmsc/upload/file/pdf/v2/lcsc/2012062037_G-Switch-PS-5850A-6PL_C963201.pdf) | Push (Latching) | 30 | 500 | 0.1185 | 1514 | 5 x 5
SS12D07VG4 087 (https://wmsc.lcsc.com/wmsc/upload/file/pdf/v2/lcsc/2201121830_SHOU-HAN-SS12D07VG4-087_C2939726.pdf) | Slide | 50 | 500 | 0.0278 | 28097 | 8 x 9
YTSPS-22E58LM (https://wmsc.lcsc.com/wmsc/upload/file/pdf/v2/lcsc/2201121900_YIYUAN-YTSPS-22E58LM_C2941005.pdf) | Push (Latching) | 50 | 500 | 0.1588 | 1705 | 5 x 8

From Table 3.3 the PS-5850A-6PL was chosen. The reasons are as follows:

- Meets regulated voltage ( > 4.2V) and regulated current ( > 400mA).
- Push switches take up less horizontal space (reduce PCB space).
- Cheapest push switch.

3.1. Design Decisions

Final design

The design choices were made to increase the efficiency of the power subsystem [3]. This includes

selected parts that were relatively cheaper when compared to similar components, consumed less current than other components/consumed as close to the required current as possible, and had smaller

dimensions which helped to reduce the size of the final PCB and in doing so helps keep the micromouse’s center of rotation as close to the front as possible.


Figure 3.1: Schematic


(a) Front PCB (with ground pours omitted for clearer view of tracks)


(b) Back PCB (with ground pours omitted for clearer view of tracks)


(c) 3D PCB (with all components populated to depict the final PCB layout)

Figure 3.2: Final PCB design layouts

3.2. Failure Management

## 3.2 Failure Management

Table 3.4: Failure Management Table

Name | Description
Track current handling [4] | Since the motors carry currents too large for standard track width, track width was increased. All tracks’ widths were increased, due to uncertainty as to which tracks would carry the highest currents.
Battery/5V Tracks | Tracks leading directly from the switch and 5V charging input were put as close to the edge of the PCB as possible to minimize any interference with other tracks. This is because they are likely to draw high currents.
Switch place-ment | Switch placed directly after the battery to ensure the entire circuit is cut off from power when the switch is on.
Switch solder bridges | Due to the vague diagram on datasheet, uncertainty arose concerning pin connections. Each connection is joined with a solder bridge to ensure the right connections are made in the future.
Additional analog voltage-divider | In case the voltage-divider output voltage is too close to the rated ADC pin, a second one was designed with a much lower output voltage (half of the maximum battery voltage)
Analog solder bridges | Both circuits are separated from battery input and pin output by solder bridges. This ensures that the correct one can be connected, whilst the unused one does not draw any current from the battery (remains completely idle).
E24 compo-nent calcula-tion rounding | All calculated E24 component values rounded to ensure the relative currents/voltages are well below rated maximums and well above rated minimums.
ERC on KiCad | After the final circuit design was chosen, the Electrical Rules Checker was run to ensure no electrical rules were broken and no avoidable errors would occur on the PCB.
DRC on KiCad | Design Rules Checker was run to ensure no design rules were broken on the PCB.

3.3. System Integration and Interfacing

## 3.3 System Integration and Interfacing

To integrate the subsystem with the rest of the system ....

Table 3.5: Interfacing specifications

J201 | Motor2_A | • Provides voltage output of Motor2_A
J202 | PWM1 | • BIN1 Logic control pin of BOUT1 (Mo-
| | tor2_A)
J203 | Motor2_B | Provides voltage output of Motor2_B
J204 | PWM2 | BIN2 Logic control pin of BOUT2 (Mo-
| | tor2_A)
J205/J206 | GND | • GND pin
J207/J208 | BATT | • Provides battery voltage
J209 | PD7 | • reserved pin
J210 | BATT_ADC | • Provides 3V3 ADC voltage
J211/J212 | 5V | • Provides 5V charging voltage
J213 | Motor1_A | Provides output voltage of Motor1_A
J214 | PWM3 | • AIN1 Logic control pin of AOUT1 (Mo-
| | tor1_A)
J215 | Motor1_B | Provides output voltage of Motor1_B
J216 | PWM4 | • AIN2 Logic control pin of AOUT2 (Mo-
| | tor1_B)

System Block Diagram


Figure 3.3: High-level block diagram showing subsystem’s link into the larger system. (Information on sensing inputs/outputs limited)

# Chapter 4
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

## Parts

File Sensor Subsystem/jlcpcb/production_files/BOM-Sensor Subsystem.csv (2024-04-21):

Comment | Designator | Footprint | LCSC
2k | RV1,RV2,RV3 | POT_3296W | C118206
0.1u | C4,C5,C6,C7,C8,C9 | C_0603_1608Metric | C14663
1u | C10,C11,C12,C13 | C_0603_1608Metric | C15849
4.7u | C1,C2,C3 | C_0603_1608Metric | C19666
1000 | R16,R17,R18 | R_0603_1608Metric | C21190
100 | R1,R10,R11,R12,R13,R14,R15,R2,R3 | R_0603_1608Metric | C22775
47k | R4,R5,R6 | R_0603_1608Metric | C25819
PT333-3B | U1,U2,U3 | LED_D5.0mm_Horizontal_O1.27mm_Z3.0mm | C5134
XC6206P332MR-G | U4,U5 | SOT-23_TOR | C5446
200 | R7,R8,R9 | R_0603_1608Metric | C8218
2N7002 | Q1,Q2,Q3 | SOT-23 | C8545
TSAL6400 | CR1,CR2,CR3 | LED_D5.0mm_Horizontal_O1.27mm_Z3.0mm | C94857

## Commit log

2024-04-21 Create Power Subsystem
    EEE3088F Power subsystem by Nicholas McFarland (MCFNIC002)
2024-04-21 Add files via upload
    Power subsystem datasheets
2024-04-21 Add files via upload
    Latex files for the power subsystem
2024-04-21 Zip files for Power subststem
2024-04-21 Add files via upload
    PDF version of Power subsystem
